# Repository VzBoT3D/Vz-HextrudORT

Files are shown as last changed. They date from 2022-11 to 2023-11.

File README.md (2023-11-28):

Buy the STD CNC version here: (https://s.click.aliexpress.com/e/_DlvB4W3)

Buy the PLUS CNC version here: (https://s.click.aliexpress.com/e/_DdyRhHl)



# The Vz-HextrudORT 

A light compact extruder that was firstly designed by MirageC. It was adapated and modified for easier printability and lower center of gravity to fit the VzBoT. 

## There 4 versions of the extruder. 
  -One printed with normal BMG type of gears
  
  -One printed with Helical grub screw gears and the rest of BMG gears
 
 (The printed version also has the possibility to have the motor at higher position to fit on the EVA 2.3-2.4 printhead)
  
  -One standard CNC version with CNC gears. Those news are not retro-compatible with BMG. Can work with 8th or 10th nema14 round motor.

  -One PLUS CNC version with bigger CNC gears.
  
  (The CNC version is smaller in Y direction, allowing more space available in the back on the VzBoT Vz-Printhead. More space to mount a motor cooler or a toolhead CANbus board etc.)
  
  Video and explanation of the Vz-HextrudORT: Vz-HextrudORT (https://youtu.be/hrsglQeEtMQ?t=952)

The 3d printed vesion project is licensed as


https://creativecommons.org/licenses/by-nc/4.0/

The CNC version is not opensource for now

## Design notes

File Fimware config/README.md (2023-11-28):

# Klipper config:

## Standard version (with smaller gears)

rotation_distance: 22  (Tune it with a 200mm extrusion test)

gear_ratio: 50:10  (For 10th motor gear)

gear_ratio: 50:8   (For 8th motor gear)

pressure_advance: 0.025  (between 0.015 to 0.035 depending on your hotend. Tuning necessary)

pressure_advance_smooth_time: 0.03

## PLUS version (with Bigger gears)

rotation_distance: 35.8  (Tune it with a 200mm extrusion test)

gear_ratio: 60:10  (For 10th motor gear)

gear_ratio: 60:8   (For 8th motor gear)

pressure_advance: 0.025  (between 0.015 to 0.05 depending on your hotend. Tuning necessary)

pressure_advance_smooth_time: 0.03

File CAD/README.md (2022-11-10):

BOM and STLs HERE : https://github.com/VzBoT3D/Vz-HextrudORT/tree/main/STLs%20and%20BOM








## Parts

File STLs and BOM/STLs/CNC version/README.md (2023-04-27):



You will need a M3x10mm for the motor mount and a M3 25mm to replace the front cover top bolt.
| Quantity | Part | Image | comment  | Links  |
| --- | ---- | --- | -----  | -----	|
| 1 | Push fit connector  | push fit connector | | https://s.click.aliexpress.com/e/_AoAejk |

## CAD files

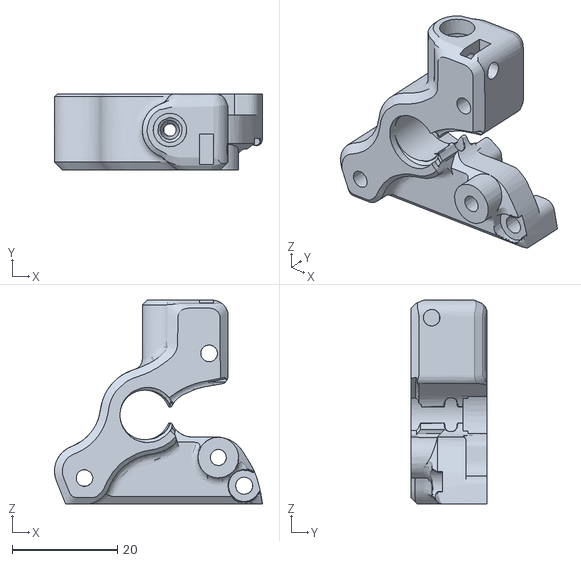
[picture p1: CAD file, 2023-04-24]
STLs and BOM/STLs/Printed versions/Main-Body-RIDGA.stl
39.5 x 14.5 x 38.7

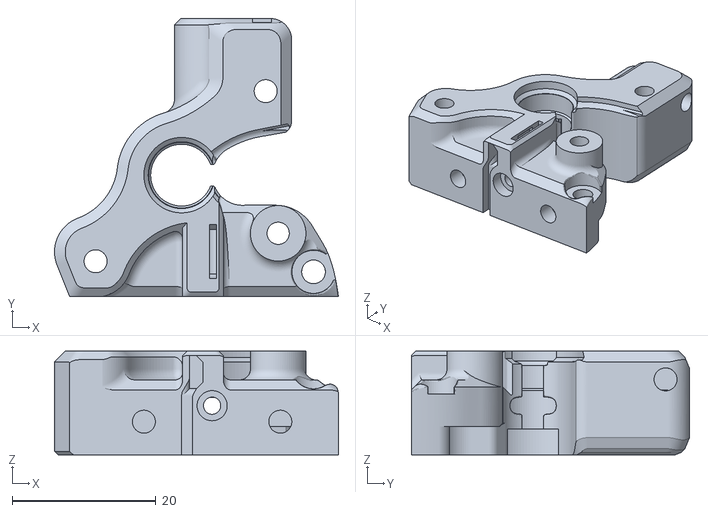
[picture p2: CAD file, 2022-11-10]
STLs and BOM/STLs/Printed versions/ERCF version/main body-ERCF.stl
39.5 x 38.7 x 14.4

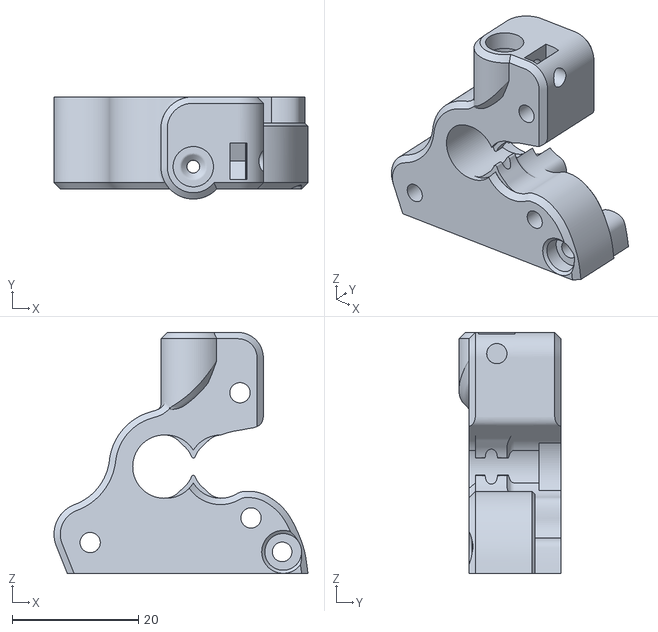
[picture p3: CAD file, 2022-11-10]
STLs and BOM/STLs/Printed versions/main body low motor helical gears.stl
40.2 x 16.1 x 38.1

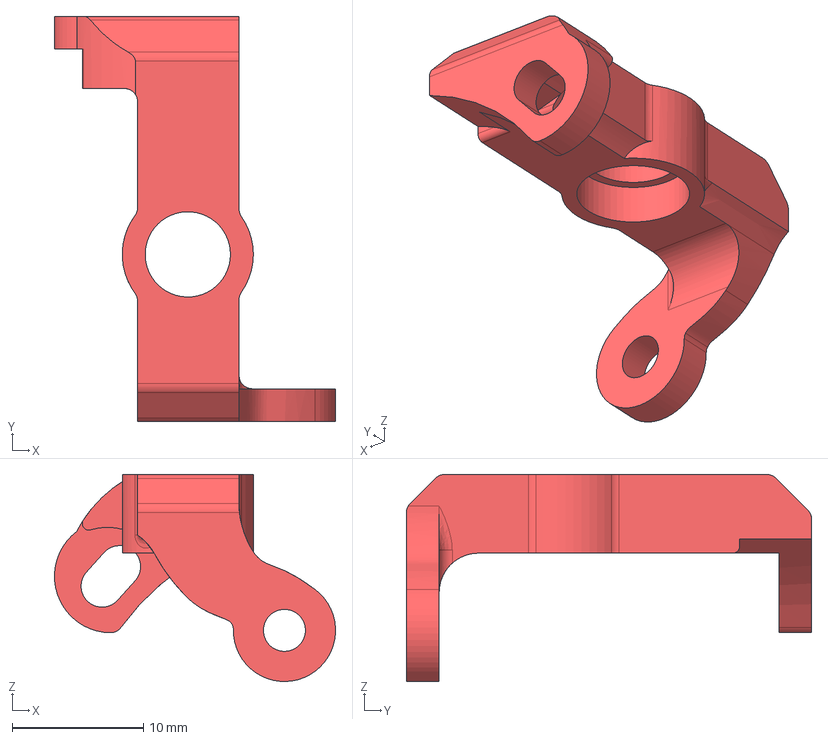
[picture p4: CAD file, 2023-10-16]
CAD/ptfe tube mount LDO.step
21.4 x 30.9 x 15.8 mm

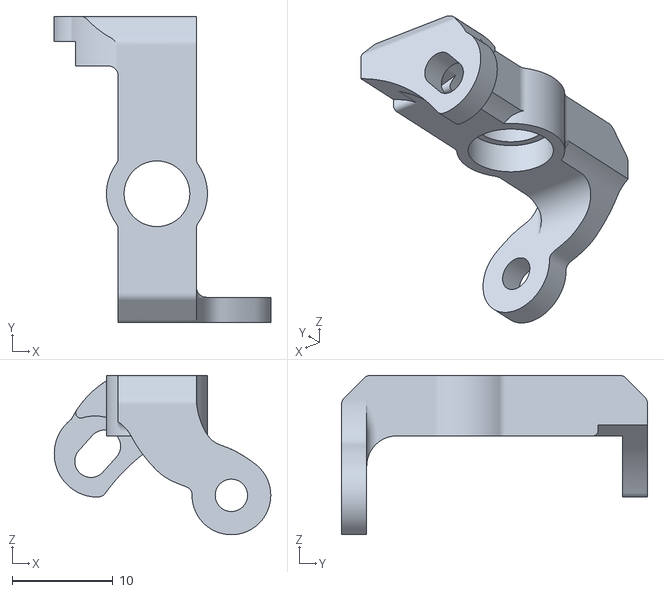
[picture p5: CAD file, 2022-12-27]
STLs and BOM/STLs/CNC version/bowden tube adapter-moon.stl
21.4 x 30.3 x 15.8

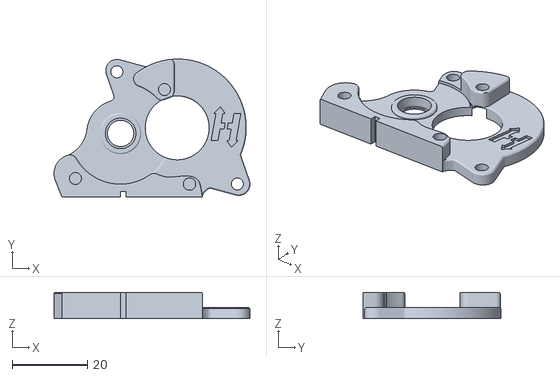
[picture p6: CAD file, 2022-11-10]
STLs and BOM/STLs/Printed versions/ERCF version/Back plate Low motor mount-ERCF.stl
52.2 x 36.7 x 7.00

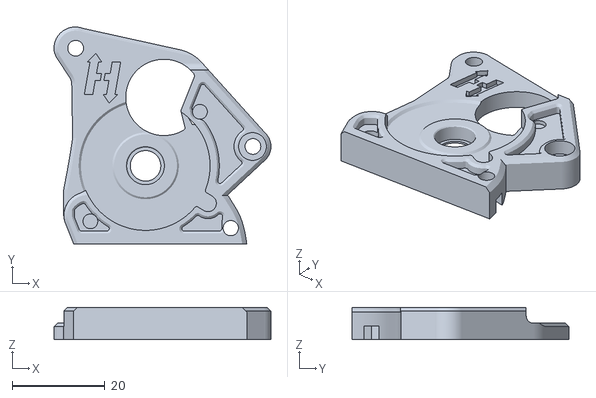
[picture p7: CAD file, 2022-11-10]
STLs and BOM/STLs/Printed versions/Back plate High motor mount.stl
46.9 x 46.9 x 7.00

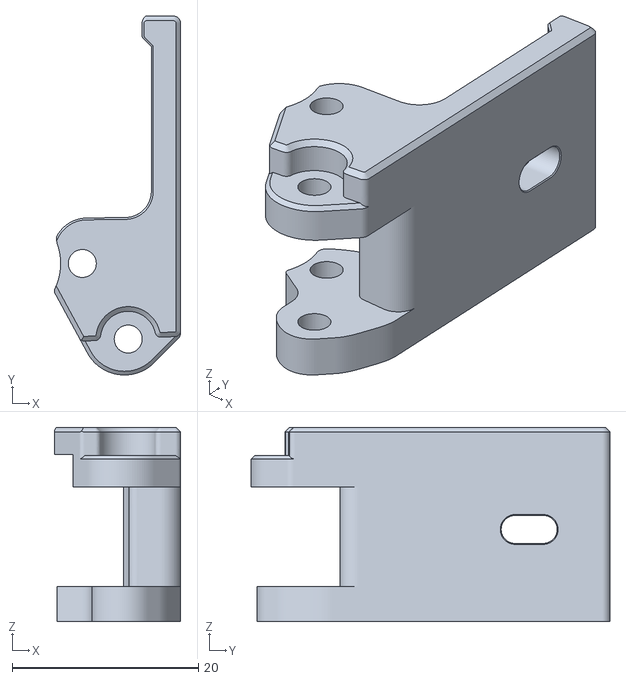
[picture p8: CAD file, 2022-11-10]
STLs and BOM/STLs/Printed versions/tension arm helical gears.stl
13.6 x 38.5 x 20.9

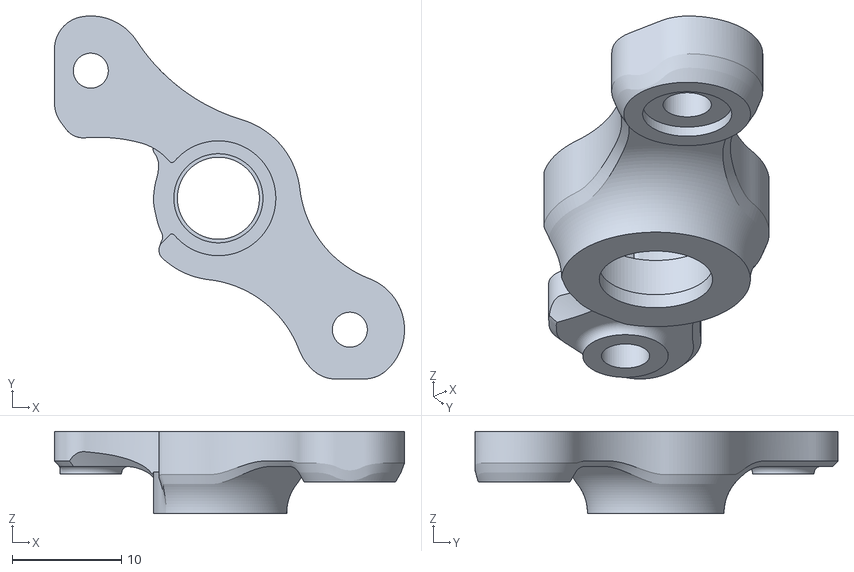
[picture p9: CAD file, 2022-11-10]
STLs and BOM/STLs/Printed versions/front cover.stl
32.0 x 33.2 x 7.50

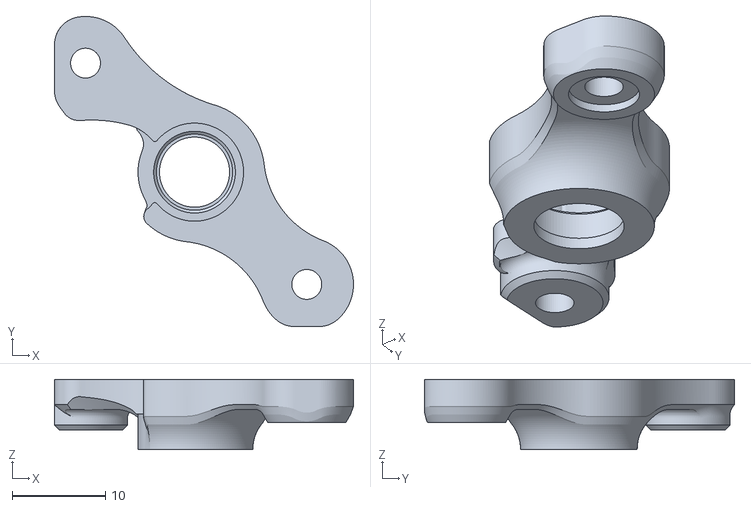
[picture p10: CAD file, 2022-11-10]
STLs and BOM/STLs/Printed versions/front cover high motor.stl
32.0 x 33.2 x 7.50

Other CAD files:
STLs and BOM/STLs/Printed versions/main body.stl
CAD/ptfe tube mount moon.step
STLs and BOM/STLs/CNC version/bowden tube adapter-LDO.stl
STLs and BOM/STLs/Printed versions/Back plate Low motor mount.stl
STLs and BOM/STLs/Printed versions/tension arm.stl

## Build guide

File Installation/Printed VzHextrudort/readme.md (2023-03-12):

All versions of the Vz-HextrudORT have the same bolting pattern. They mount can be mounted from the bottom of the extruder using M3 bolts. The spacing between the mounting holes is 19mm, exactly the same as the LGX Lite.

You will also need a piece of a PTFE tube between the extruder and the hotend. The lenght vary depending on the extruder and the mounting option.

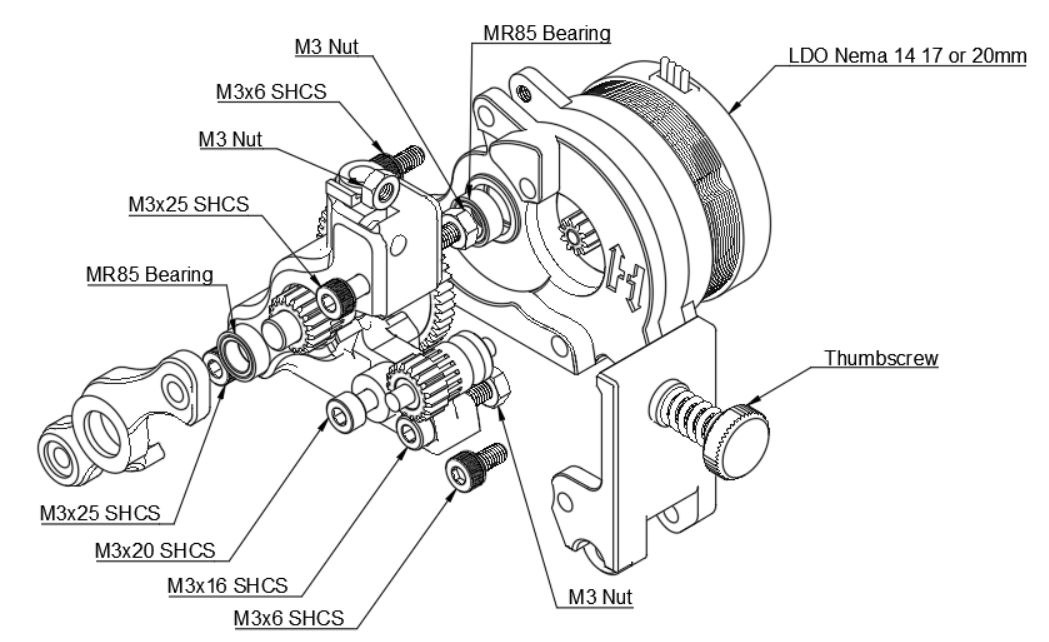
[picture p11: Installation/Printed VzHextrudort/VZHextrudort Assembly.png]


| Quantity | Part | Image | comment  | Links  |
| --- | ---- | --- | -----  | -----	|
| 1 | Push fit connector  | push fit connector | | https://s.click.aliexpress.com/e/_AoAejk |
| 1 | LDO Nema 14 17-20mm |  | | https://s.click.aliexpress.com/e/_Dcwpt5T |
| 1 | BMG Gear set |  | |https://s.click.aliexpress.com/e/_DCNS1qz |
| 2 | M3 Nut | | | |
| 2 | M3x6 SHCS | | | |
| 2 | M3x25 SHCS | | | |
| 1 | M3x20 SHCS | | | |
| 1 | M3x16 SHCS | | | |

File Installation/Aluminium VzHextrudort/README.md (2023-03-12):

# Mounting
All versions of the Vz-HextrudORT have the same bolting pattern. They mount can be mounted from the bottom of the extruder using M3 bolts. The spacing between the mounting holes is 19mm, exactly the same as the LGX Lite.





You will also need a piece of a PTFE tube between the extruder and the hotend. The lenght vary depending on the extruder and the mounting option.

# Alignment:

- It is important to have the main shaft/gear parallel to the idler and to the main body. There is a tiny bit of play/tolerance in the front cover and back plate assembly that can cause wobbling issue if not align properly. To align it properly follow these steps:

1-Make sure tension is on the tension arm

2-Loosen the 2 motor bolts

3-Insert filament in the extruder and make sure the filament is loaded up all the way to the grub gears.

4-Loosen the 2 front cover bolts and the 3rd lower right front bolt 

5-Tighten all 3 bolts

6-Adjust motor position so there is not too much pressure on the POM gear and tighten the 2 bolts. (Having the motor pinion gear too tight on the POM gear can cause issue.)

# PTFE tube retainer:

- If you wish to add a retaning push fit connector. You can print the adpter fround in the STL folder. There are 2 versions. One for Moon motors, and one for LDO motors. You will need a longer M3 bolt for the motor and a M3 nut


| Quantity | Part | Image | comment  | Links  |
| --- | ---- | --- | -----  | -----	|
| 1 | Push fit connector  | push fit connector | | https://s.click.aliexpress.com/e/_AoAejk |

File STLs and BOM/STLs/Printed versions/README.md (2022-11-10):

### Helical version will use the same back plate, same front cover, same hardware except the 2 feed gears (helical). The main body and tension arm are different.






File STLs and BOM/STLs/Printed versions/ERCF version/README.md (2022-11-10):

# This Vz-HextrudORT has extra hall sensor to work with the Enraged Rabbit Carrot Feeder project.
https://github.com/EtteGit/EnragedRabbitProject

BOM (Please refer to the Github project for the BOM:
-Hall sensor
-M3 washer
-Magnet6x3





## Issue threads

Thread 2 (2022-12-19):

Inconsistent extrusion - visible wood grain

agentk, 2022-12-19:
Hey Simon, loved how easy the Mellow Vz-Hextrudort CNC was to install and setup on a Trident with Dirtybird hotend.

Is there anything I should be looking to mitigate visible wood grain when printing Mihai's Inconsistent Extrusion Test? The Vz-Hextrudort surface finish is the smoothest of three extruders I have on hand (LGX Lite, and a SLS Sherpa Micro), but it's the only one with the wood grain visible.

I purchased two Vz-Hextrudorts with the included motor and both have the exact same finish.

Photo of the grain only difference between the two photos is microsteps 8 vs 32.
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

agentk, 2022-12-19:
Update. Vz-Hextrudort is 100% not the issue. It's the 8T Moons motor that came with it in the bundle from Mellow. I swapped it for an LDO pancake and the issue is completely gone away. These prints are now even smoother than the same motor on a LGX Lite.

1000% recommend the Vz-Hextrudort CNC 😍.

Left: 8T Moons motor, Right: 10T LDO motor
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

Closed 2022-12-19.

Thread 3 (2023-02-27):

3d Print Optimizations

Moulebutz, 2023-02-27:
-When printing with 0.4 Nozzle some features would benefit from being beefed up(here in Red)
 Especially the **main_body** bottom right hole is having a hard time being sliced, even with thin walls active.
-Orange sections could be optimized to fit 2 perimeters inside by slightly thicken the model.
-I simplified the bottom right motor mount a little to optimize it for 3d printing. (in green)
-I also extruded the **main_body** lower right hole by 1mm to be able to fir a 16mm screw since they're more common.

-please update CAD to latest Version (doesn't match witch stl's

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

Closed 2025-01-02.

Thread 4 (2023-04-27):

Please remove PTFE tube from STEP file.

edspeds, 2023-04-27:
The PTFE tube in the STEP file can be a nuisance when trying to model an extruder assembly around the Vz-Hextrudort and my CAD software is unable to remove the PTFE tube from the STEP file.  Would it be possible to get a model without the PTFE tube attached?  I get you're not wanting to share too much IP but struggled to work around the PTFE for my needs.  As an aside I made worked up a smaller Bowden adapter for it as well that might interest some...

https://www.printables.com/model/420994-bowden-clip-adapter-for-vz-hextrudort-cnc

pbsuper, 2025-01-02:
could you post that bowden clip on [Usermods](https://github.com/VzBoT3D/VzBoT-UserMods) so that it's easy to find for users?

edspeds, 2025-01-03:
Will try right now account is requiring 2FA code but I never set up 2FA so I’m going in circles with support trying to regain access to my account On Jan 2, 2025, at 12:00 PM, pbsuper ***@***.***> wrote:
could you post that bowden clip on Usermods so that it's easy to find for users?

—Reply to this email directly, view it on GitHub, or unsubscribe.You are receiving this because you authored the thread.Message ID: ***@***.***>

edspeds, 2025-01-11:
Okay I uploaded the files but being that I use a Jubilee I’m uncertain if it’s compatible with the Vz330 or Vz235.  I checked that it is but don’t know for sure.  Hopefully you can review and correct as needed.

Ed

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

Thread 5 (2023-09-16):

Filament insert problem

TypQxQ, 2023-09-16:
I wanted to use my VZ-Hextrudort for my ERCF printhead but the filament is not entering the extruder smoothly. It has a flat surface instead of a chamfer where the filament enters and it gets stuck here. Also by hand it's hard to hit that hole. Is there anything I can do to ease it in?
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

TypQxQ, 2023-10-25:
I made the insertion easier by using a short Capricorn tube with small inner diameter between the opening in the extruder and a PTFE tube retainer. I use 2.5mm id for my reverse bowden and Capricorn between extruder and hotend.

Closed 2025-01-02.

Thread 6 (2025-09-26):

Whats the state of the twill extruder gear or helical gear

skuep, 2025-09-26:
I have a standard Vz-Hextrudort CNC from ages ago (from Mellow) and it works pretty well. It has the advertised twill extruder gears and helical gears.
I wanted to try the CNC Plus variant from Mellow, but it seems like its impossible to get one with the same gear design. They all come with straight gears now, despite the AliExpress image showing otherwise.

Whats the deal here? Have there been issues with the twill design? I asked Mellow and they said, that the straight gears is an "upgrade", which sounds dubious to me.

Best Regards

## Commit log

2022-11-10 changed step to zip in cad
2022-12-27 Adding push fit PTFE mount
    [Back plate High motor mount.stl, Back plate Low motor mount-ERCF.stl, Back plate Low motor mount.stl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]
2023-03-12 Seperation Printed and Aluminum installation
2023-10-16 Adding CAD file for PTFE tube retainer
    [ptfe tube mount LDO.step, ptfe tube mount moon.step]
2025-01-03 Create Goliath short +WC vz-hextrudort.step
    added WC Vzhex Cad.
